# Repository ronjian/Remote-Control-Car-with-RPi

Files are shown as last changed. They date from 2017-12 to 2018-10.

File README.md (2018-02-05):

<h2 id='circuit'>Demo</h2>

<h2 id='component'>Component list</h2>

Here are the components I prepared, most I bought on Taobao. Here I give Amazon link for reference.  
- 1 * [L298N Motor Drive Controller Board](https://www.amazon.com/Qunqi-Controller-Module-Stepper-Arduino/dp/B014KMHSW6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)
- 4 * [HC-SR04 Ranging Detector / Ultrasonic Sensor](https://www.amazon.com/SainSmart-HC-SR04-Ranging-Detector-Distance/dp/B004U8TOE6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)
- 5 * [SG90 Micro Servo Motor](https://www.amazon.com/J-Deal%C2%AE-Micro-Helicopter-Airplane-Controls/dp/B00X7CJZWM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)
- 2 * [400-point Experiment Breadboard](https://www.amazon.com/microtivity-400-point-Experiment-Breadboard-Jumper/dp/B004RXKWDQ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)
- 1 * [5v 2a battery bank](https://www.amazon.com/KMASHI-15000mAh-External-Portable-Powerful/dp/B00JP8MZGK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)
- 2 * [18650 Li-ion battery](https://www.amazon.com/Panasonic-NCR18650B-Rechargeable-Battery-Transport/dp/B01C4GFVN8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)
- 1 * [Portable Wireless Bluetooth Speaker](https://www.amazon.com/A2-LENRUE-Bluetooth-Handsfree-Smartphone/dp/B071WYXY6B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)
- 1 * [RPi CSI camera](https://www.amazon.com/Arducam-Megapixels-Sensor-OV5647-Raspberry/dp/B012V1HEP4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)
- 1 * [camera extension cable 50cm](https://www.amazon.com/Miuzei-Extension-Ribbon-Raspberry-Camera/dp/B072N7VXPR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)
- 1 * [T Type GPIO Adapter](https://www.amazon.com/Kuman-Breakout-Expansion-Assembled-Raspberry/dp/B0761NYF6Y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)
- 1 * [Battery Storage Case for 2 X 18650 battery](https://www.amazon.com/SACKORANGE-Plastic-Battery-Storage-Holder/dp/B06XT1DM74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)
- 1 * [Camera Mount](https://www.amazon.com/Platform-Anti-Vibration-Dampener-Quadcopter-Crazepony/dp/B075N6TPWL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)
- 1 * [Misc, suggest such kind package](https://www.amazon.com/Elegoo-EL-CK-002-Electronic-Breadboard-Potentiometer/dp/B01ERP6WL4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)
- 1 * [RPi 3 b+](https://www.amazon.com/Raspberry-Pi-RASPBERRYPI3-MODB-1GB-Model-Motherboard/dp/B01CD5VC92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)
- 1 * RC car kit

<h2 id='circuit'>Circuit diagram</h2>

<p align="center">
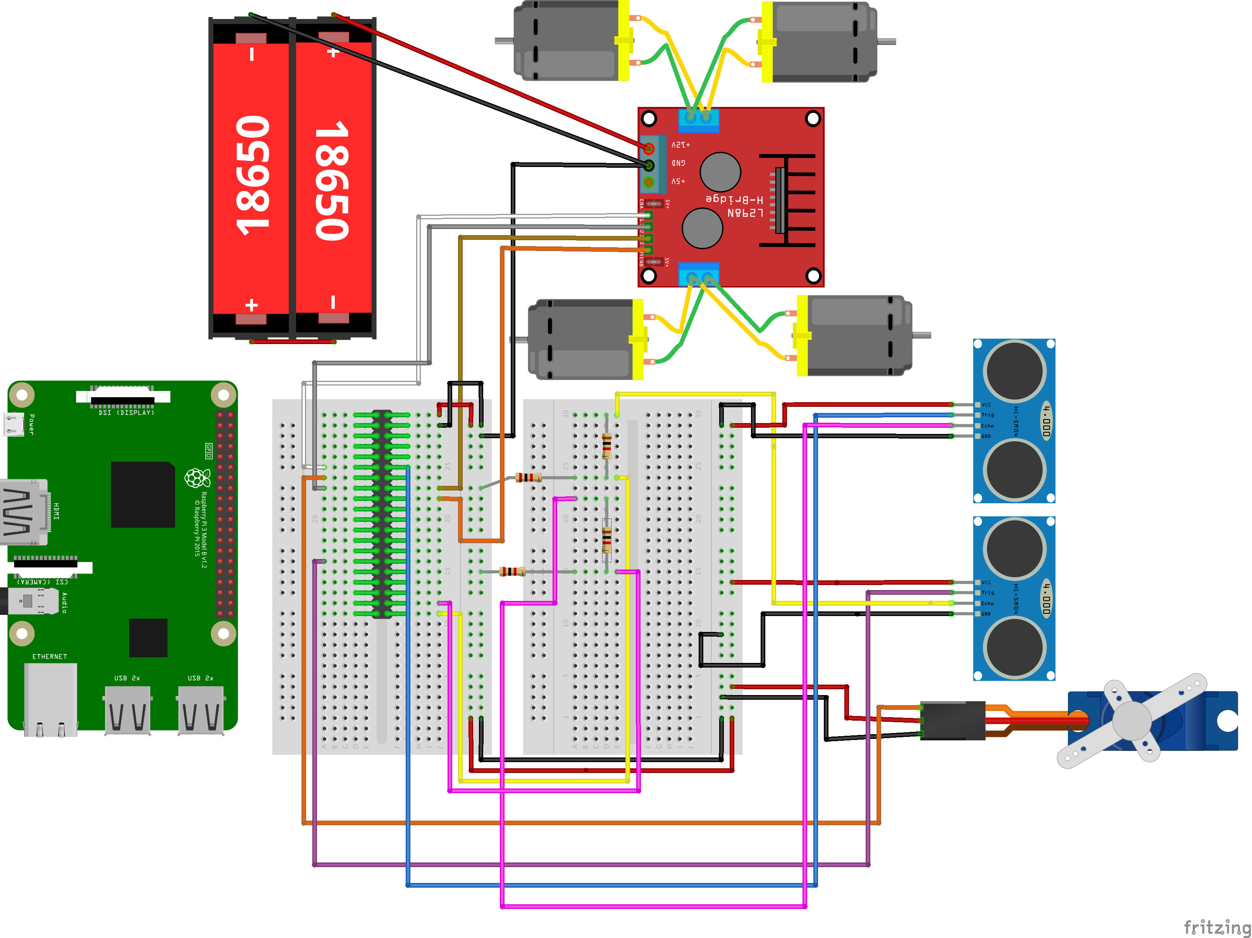
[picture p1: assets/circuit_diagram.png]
<br>
</p>

Please notes:  
- I don't draw out the audio player, camera, which are easy to be plunge in by yourself.
- I just draw out one servo and two ultra sonic sensor to keep the diagram clear.  
- In realistic, I have a T-Type GPIO Adapter like below mapping the GPIO pins to the breadboard, so in the diagram, I place a RPi header on the left side breadboard.
- [Here](./Reference.md#l298n) is more detail about L298N dirver.
- [Here](./Reference.md#HC-SR04) is more detail about HC-SR04 ultrasonic sensor.

<p align="left">
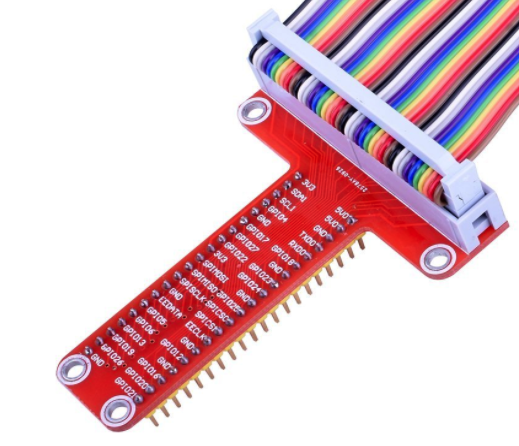
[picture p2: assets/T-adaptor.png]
<br>
</p>

I suggest checking the _Fritzing_sketch.fzz_ by [Fritzing](http://fritzing.org/home/) app.

<h2 id='introduction'>Brief introduction</h2>
This project is built on python3.  

- dependencies: [flask](http://flask.pocoo.org/), [RPi.GPIO](https://sourceforge.net/p/raspberry-gpio-python/wiki/install/), [pigpio](http://abyz.me.uk/rpi/pigpio/index.html), [picamera](https://picamera.readthedocs.io/en/release-1.13/) [pimodules](https://github.com/ronjian/pimodules)
- [Here](./Reference.md) is all the reference resources I collected during the project. Maybe you can find something I miss to mention here.
- Start server, then check ```http://192.168.1.110:2000/```(replace IP address with yours) in your browser:  
```shell
python3 ./src/main/server.py
```
- [This](./camera_streamer_manual.md) is a manual to setup mjpg steamer on RPi, which is another popular option to feed camera video. If you only want the streaming video on RPi.
- I use sublime sftp tool to sync codes between my laptop and Pi. [tutorial here](https://www.youtube.com/watch?v=g6NqBGHFfm0)

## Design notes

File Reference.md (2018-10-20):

<h2 id='gpio'>RPI3 GPIO Pin Mappings</h2>

https://pinout.xyz/

<p align="center">
<br>
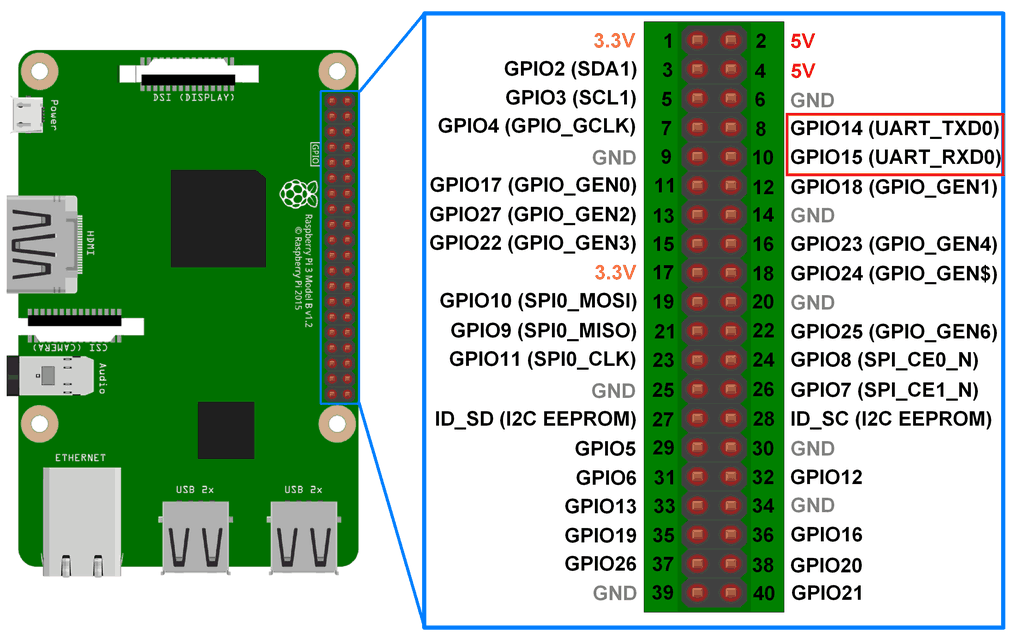
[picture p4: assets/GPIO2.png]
<br>
</p>

<h2 id='l298n'>Control motors by L298N</h2>

* Basic usage of L298N to control motors forward and backward:
    * http://www.piddlerintheroot.com/l298n-dual-h-bridge/
    * http://www.explainingcomputers.com/rasp_pi_robotics.html    
* Programming to use keyborad to control the motors:
    * Python curses package: https://docs.python.org/2/library/curses.html#constants  
    
There is two ways to control the motor speed. One is PWM changing on the INPUT pin as the below code snippet.
The other is using the enable PIN to change PWM, as [this code](https://github.com/custom-build-robots/Motor-Driver-L298N-H-Bridge/blob/master/L298NHBridge.py)
implemented. There is a [post](https://www.raspberrypi.org/forums/viewtopic.php?f=37&t=90243) comparing these two solutions.  
```python
#!/usr/bin/env python3
"""infinitely loop the motor to speed up and down"""
import time
import RPi.GPIO as GPIO
GPIO.setmode(GPIO.BCM)
GPIO.setup(23, GPIO.OUT)
GPIO.setup(24, GPIO.OUT)
p = GPIO.PWM(23, 50) 
p.start(0)
GPIO.output(24, False)
try:
    while 1:
    	# low to high
        for dc in range(0, 101, 5):
            p.ChangeDutyCycle(dc)
            time.sleep(0.2)
        # high to low
        for dc in range(100, -1, -5):
            p.ChangeDutyCycle(dc)
            time.sleep(0.2)
except KeyboardInterrupt:
    pass
p.stop()
GPIO.cleanup()
```
* check [here](http://www.toptechboy.com/raspberry-pi/raspberry-pi-lesson-27-analog-voltages-using-gpio-pwm-in-python/)
for PWM programming on RPi. [GPIO document](https://sourceforge.net/p/raspberry-gpio-python/wiki/PWM/) here.
[pigpio package](http://abyz.me.uk/rpi/pigpio/python.html) also implements controling PWM.

<h2 id='DHT11'>DHT11</h2>

Example code and tutorial:  
http://osoyoo.com/2017/03/21/%E6%A0%91%E8%8E%93%E6%B4%BE%E8%AF%BB%E5%8F%96dht11/  
<p align="center">
Diagram<br>
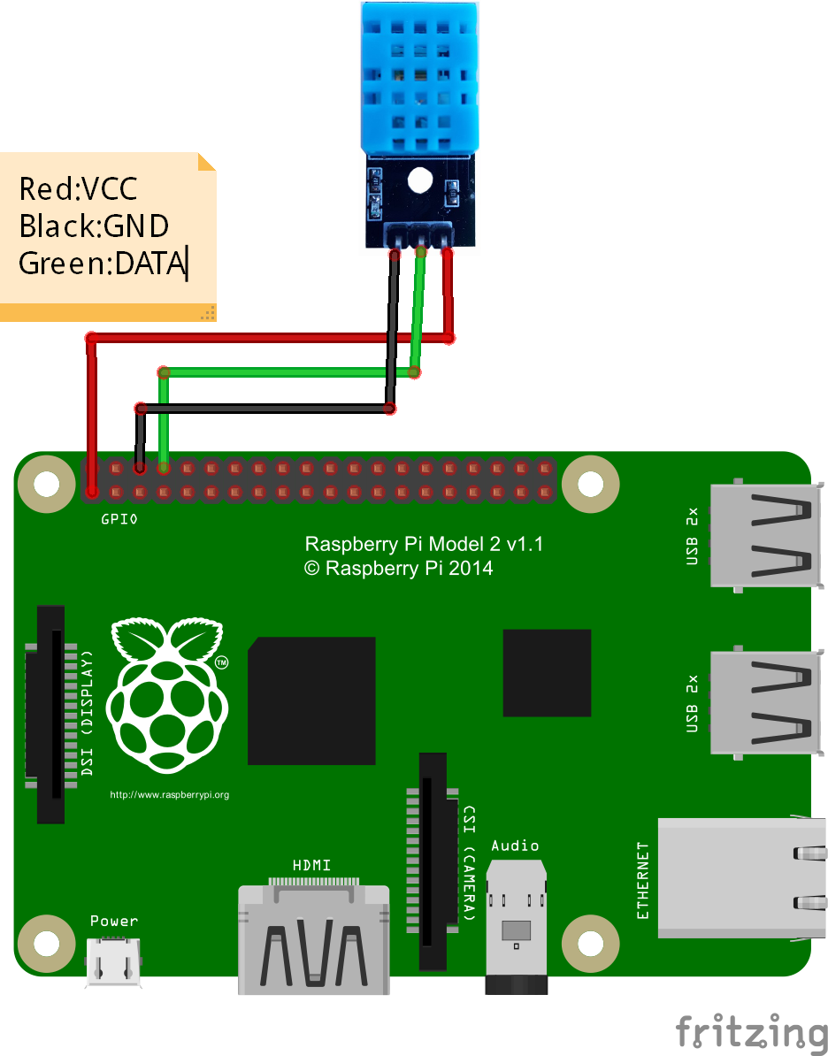
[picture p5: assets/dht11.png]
<br>
Demo<br>
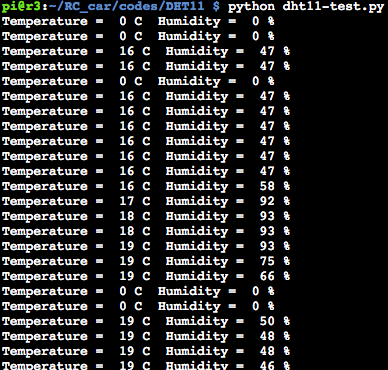
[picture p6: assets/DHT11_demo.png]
<br>
</p>

<h2 id='TCRT5000'>TCRT5000</h2>

Example code and tutorial:  
* https://raspberrytips.nl/tcrt5000/  
* https://github.com/the-raspberry-pi-guy/robot  

<p align="center">
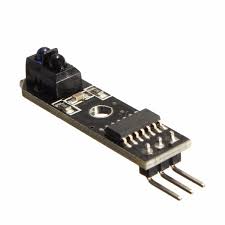
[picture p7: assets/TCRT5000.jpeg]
<br>
Demo<br>
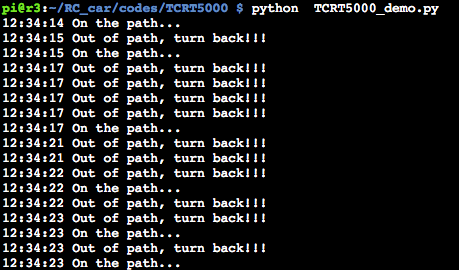
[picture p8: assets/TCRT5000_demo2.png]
<br>
</p>

<h2 id="servo">Servo</h2>

* tutorial:  
    * Servo control: https://www.youtube.com/watch?v=N5QmZ92uvUo  
    * Servo platform installation: http://v.youku.com/v_show/id_XODk3NDE1NjYw.html  

<h2 id='HC-SR04'>HC-SR04 Ultrasonic Rangefinder</h2>

reference:  
* https://www.youtube.com/watch?v=sXJjfEisjpo  
* https://www.modmypi.com/blog/hc-sr04-ultrasonic-range-sensor-on-the-raspberry-pi  
* https://raspberrytips.nl/hc-sr04-ultrasone-sensor/  
* https://gist.github.com/raspberrytipsnl/85cb7807340bede2279b12f950aef5cb  
* https://stackoverflow.com/questions/45488233/controlling-continuous-servo-using-python-in-raspberry-pi-but-the-continuous-ser

<p align="center">
Circuit diagram<br>
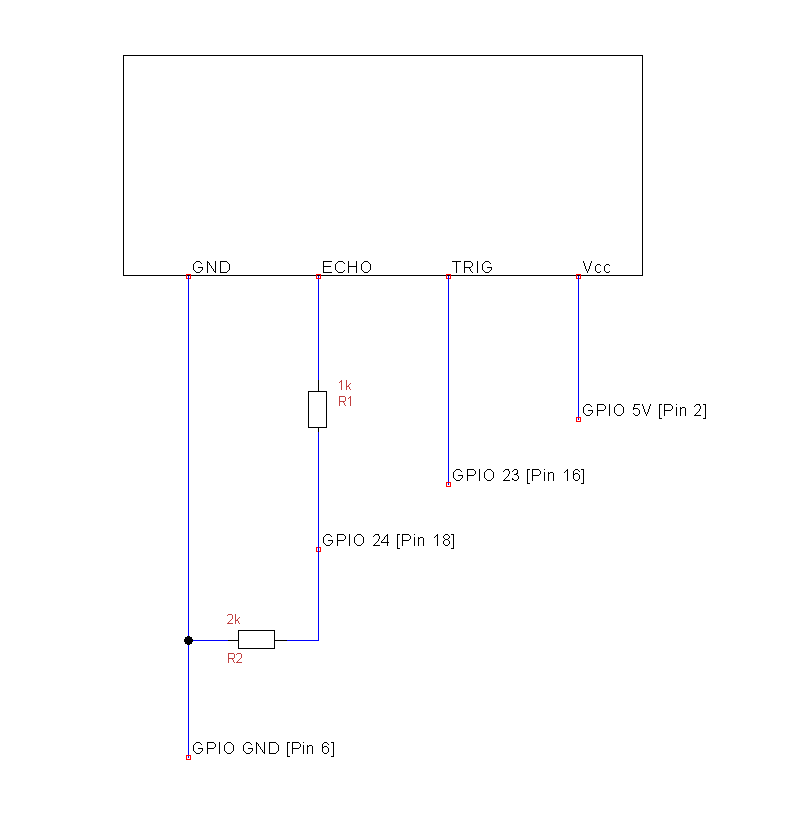
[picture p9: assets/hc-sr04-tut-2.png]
<br>
Implementation<br>
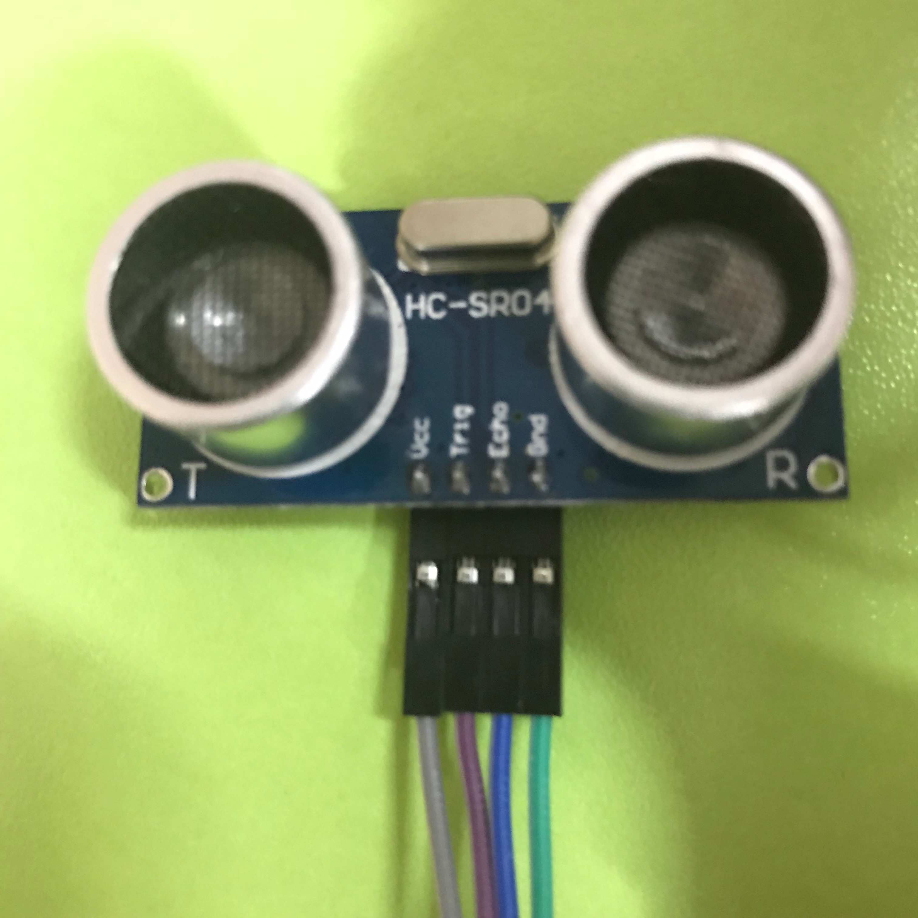
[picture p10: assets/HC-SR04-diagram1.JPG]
<br>
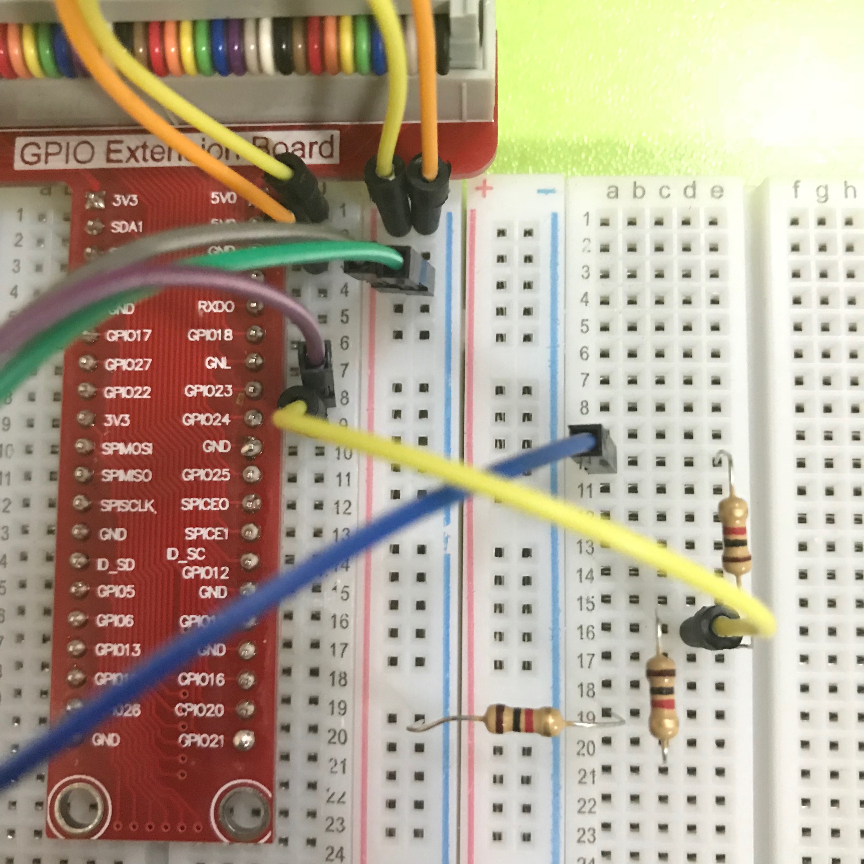
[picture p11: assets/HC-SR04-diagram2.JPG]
<br>  
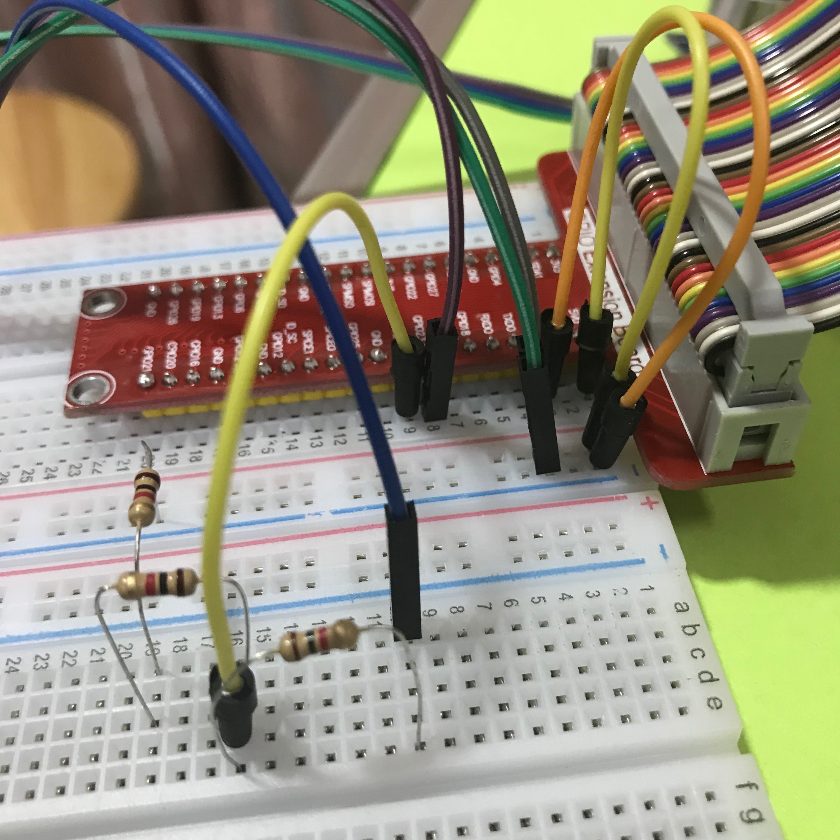
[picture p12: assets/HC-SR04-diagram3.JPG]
<br>  
Demo<br>
<br>  
</p>

<h2 id='Flask_Web_Server'>Flask Web Server</h2>

* https://randomnerdtutorials.com/raspberry-pi-web-server-using-flask-to-control-gpios/  
* http://mattrichardson.com/Raspberry-Pi-Flask/
* http://nessy.info/?p=1136
* http://vladikk.com/2013/09/12/serving-flask-with-nginx-on-ubuntu/  

<h2 id="NRF24L01">NRF24L01</h2>

* http://thezanshow.com/electronics-tutorials/raspberry-pi/tutorial-32-33  
* https://github.com/BLavery/lib_nrf24  
* SPI and I2C tutorial: https://learn.sparkfun.com/tutorials/raspberry-pi-spi-and-i2c-tutorial

<h2 id='KY-037'>KY-037</h2>

reference:  
http://sensorkit.en.joy-it.net/index.php?title=KY-037_Microphone_sensor_module_(high_sensitivity)  
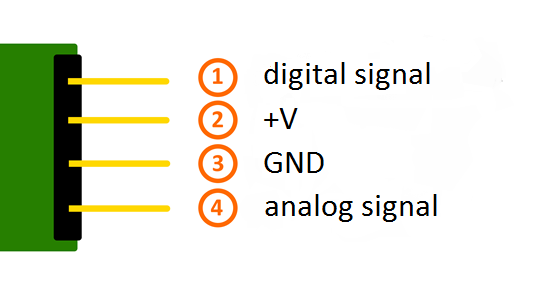
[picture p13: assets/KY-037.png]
<br>

<h2 id='FC-04'>FC-04</h2>

reference:
http://www.instructables.com/id/Using-a-sound-sensor-with-a-Raspberry-Pi-to-contro/

<h2 id='sound'>Sound Detector</h2>

reference:  
https://www.youtube.com/watch?v=GiXNUYPrQ7I  

<h2 id='heart_rate'>Heart Rate module</h2>

* MCP3008 is required
* https://pulsesensor.com/

<h2 id='speaking'>Make RPi speak</h2>

Setting ```audio_pwm_mode=2``` in ```/boot/config.txt``` can reduce the background noise for audio from 3.5mm jack.

If you want to set usb sound card for RPi3 as default sound output.  
- check the device number by ```aplay -l```  
- add below lines to ```/etc/asound.conf```   
```
pcm.!default {
    type hw
    card 1
}

ctl.!default {
    type hw           
    card 1
}
```

- verify as:

```aplay -D plughw:1,0  /usr/share/sounds/alsa/*```

```omxplayer -b -o alsa:hw:1,0  xxx.mp3```

Install ```espeak``` on RPi, refer to: 

- https://www.dexterindustries.com/howto/make-your-raspberry-pi-speak/
- https://www.devdungeon.com/content/text-speech-python-espeak

- volumn control:  
http://blog.scphillips.com/posts/2013/01/sound-configuration-on-raspberry-pi-with-alsa/

- Install espeak lib for python3 as 
```sudo apt-get install espeak python-espeak```

<h2 id='pi-shutdown-button'>Control Pi start, shutdown, reboot with one button</h2>

- https://gilyes.com/pi-shutdown-button/
- threaded callback function: https://sourceforge.net/p/raspberry-gpio-python/wiki/Inputs/

<h2 id="camera">Camera</h2>

- Amazing recipes for RPi camera: https://picamera.readthedocs.io/en/release-1.13/recipes1.html
- Flask server solution to stream camera video: https://github.com/miguelgrinberg/flask-video-streaming

<h2 id='KY-022'>KY-022(IR sensor)</h2>

reference:  
- wire connection: http://sensorkit.en.joy-it.net/index.php?title=KY-022_Infrared_receiver_module#Code_example_Raspberry_Pi
- IR receiver code in python: http://abyz.me.uk/rpi/pigpio/examples.html#Python%20code (see "IR Receiver")

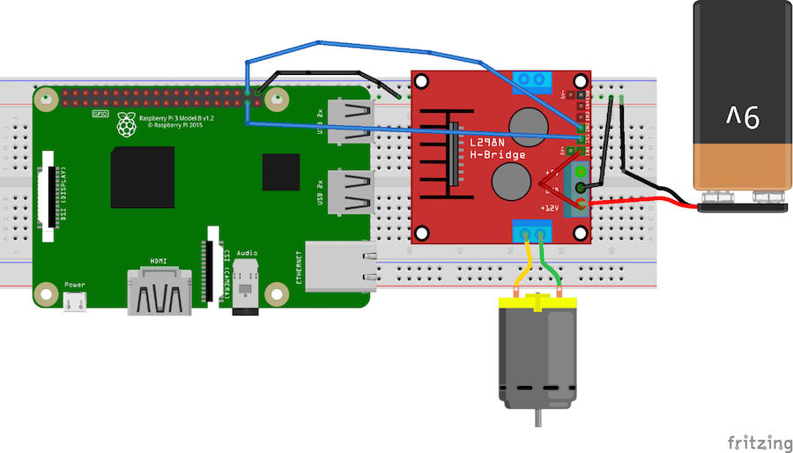
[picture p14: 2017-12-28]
assets/Raspberry-Pi-L298-Schematic.png

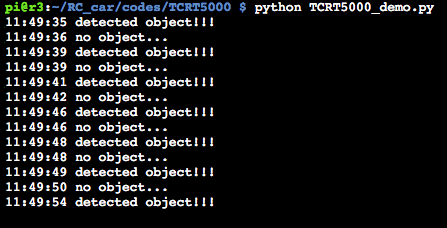
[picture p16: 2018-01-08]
assets/TCRT5000_demo.png

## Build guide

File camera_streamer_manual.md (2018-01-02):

# Steps to stream the Raspberry Pi camera video to client browser in the WIFI enviroment.
Refer to this post for detail: http://petrkout.com/electronics/low-latency-0-4-s-video-streaming-from-raspberry-pi-mjpeg-streamer-opencv/  
Do below steps on the Raspberry Pi (Mine is Raspberry Pi 3 Model B):  
```shell
mkdir mjpg-streamer
cd mjpg-streamer
git clone https://github.com/jacksonliam/mjpg-streamer.git .
cd mjpg-streamer-experimental
make
export LD_LIBRARY_PATH=.
./mjpg_streamer -o "output_http.so -w ./www" -i "input_raspicam.so -x 640 -y 480 -fps 20 -ex night -rot 180"
```  
Check the browser via url ```http://r3:8080/?action=stream```, 
```r3``` is my Pi's hostname in the internel network, Ip address like ```192.168.31.110``` also works fine.  
### Demo:
<p align="center">
<img src="assets/infinite.png" width=700/>
<p/>

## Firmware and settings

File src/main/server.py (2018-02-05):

from flask import Flask, render_template, request, Response
from pimodules import motor, servo_hw, ultrasonic
import obstacle_avoidance
from time import sleep
import threading
from pathlib import Path
from camera.camera_pi import Camera

app = Flask(__name__)

@app.route("/")
def index():
    return render_template('index.html')

def gen(camera):
    """Video streaming generator function."""
    while True:
        frame = camera.get_frame()
        yield (b'--frame\r\n'
               b'Content-Type: image/jpeg\r\n\r\n' + frame + b'\r\n')

@app.route('/video_feed')
def video_feed():
    """Video streaming route. Put this in the src attribute of an img tag."""
    return Response(gen(Camera()),
                    mimetype='multipart/x-mixed-replace; boundary=frame')

@app.route("/forward")
def forward():
    speed_pct = int(request.args.get('speed_pct'))
    motor_control.forward(speed_pct)
    return "OK"
 
@app.route("/backward")
def backward():
    speed_pct = int(request.args.get('speed_pct'))
    motor_control.backward(speed_pct)
    return "OK"

@app.route("/turn_left")
def turn_left():
    speed_pct = int(request.args.get('speed_pct'))
    motor_control.left(speed_pct)
    return "OK"
 
@app.route("/turn_right")
def turn_right():
    speed_pct = int(request.args.get('speed_pct'))
    motor_control.right(speed_pct)
    return "OK"

@app.route("/stop")
def stop():
    motor_control.stop()
    return "OK"

@app.route("/camera_up")
def camera_up():
    camera_vertical_servo.step_move(direction = -1.0)
    return "OK"
 
@app.route("/camera_down")
def camera_down():
    camera_vertical_servo.step_move(direction = 1.0)
    return "OK"

@app.route("/camera_left")
def camera_left():
    camera_horizontal_servo.step_move(direction = 1.0)
    return "OK"
 
@app.route("/camera_right")
def camera_right():
    camera_horizontal_servo.step_move(direction = -1.0)
    return "OK"

@app.route("/camera_reset")
def camera_reset():
    camera_vertical_servo.reset()
    camera_horizontal_servo.reset()
    return "OK"

@app.route("/take_photo")
def take_photo():
    pass
    return "OK"

@app.route("/back_uc_left")
def back_uc_left():
    back_servo.step_move(direction = 1.0)
    return "OK"
 
@app.route("/back_uc_right")
def back_uc_right():
    back_servo.step_move(direction = -1.0)
    return "OK"

@app.route("/back_uc_reset")
def back_uc_reset():
    back_servo.reset()
    return "OK"

@app.route("/back_distance")
def back_distance():
    print("Back distance is %f cm" % back_ultrasonic.detect())
    return "OK"

@app.route("/left_uc_left")
def left_uc_left():
    left_servo.step_move(direction = 1.0)
    return "OK"
 
@app.route("/left_uc_right")
def left_uc_right():
    left_servo.step_move(direction = -1.0)
    return "OK"

@app.route("/left_uc_reset")
def left_uc_reset():
    left_servo.reset()
    return "OK"

@app.route("/left_distance")
def left_distance():
    print("Left distance is %f cm" % left_ultrasonic.detect())
    return "OK"

@app.route("/right_uc_left")
def right_uc_left():
    right_servo.step_move(direction = 1.0)
    return "OK"
 
@app.route("/right_uc_right")
def right_uc_right():
    right_servo.step_move(direction = -1.0)
    return "OK"

@app.route("/right_uc_reset")
def right_uc_reset():
    right_servo.reset()
    return "OK"

@app.route("/right_distance")
def right_distance():
    print("Right distance is %f cm" % right_ultrasonic.detect())
    return "OK"

@app.route("/obstacle_avoiding_start")
def obstacle_avoiding_start():
    stop_instances()
    if oa_signal_path.exists(): oa_signal_path.unlink()
    t = threading.Thread(target=obstacle_avoidance.start)
    t.start()
    print("thread kick off")
    return "OK"

@app.route("/obstacle_avoiding_stop")
def obstacle_avoiding_stop(restart=True):
    oa_signal_path.touch()
    print("sent the stop signal")
    if restart:
        while oa_signal_path.exists():
            sleep(1)
        print("obstacle_avoiding stopped, restarting instances")
        start_instances()
    return "OK"

def start_instances():
    motor_control.start()
    back_ultrasonic.start()
    right_ultrasonic.start()
    left_ultrasonic.start()
    right_servo.start()
    camera_vertical_servo.start()
    camera_horizontal_servo.start()
    left_servo.start()
    back_servo.start()
    
def stop_instances():
    # make sure to close servos first
    camera_vertical_servo.close()
    camera_horizontal_servo.close()
    back_servo.close()
    left_servo.close()
    right_servo.close()
    right_ultrasonic.close()
    motor_control.close()
    back_ultrasonic.close()
    left_ultrasonic.close()

if __name__ == "__main__":
    try:
        STRIDE=0.05
        motor_control = motor.CONTROL(RIGHT_FRONT_PIN=17, LEFT_FRONT_PIN=23, RIGHT_BACK_PIN=22, LEFT_BACK_PIN=24)
        back_ultrasonic = ultrasonic.CONTROL(TRIG = 6, ECHO = 13)
        right_ultrasonic = ultrasonic.CONTROL(TRIG = 5, ECHO = 21)
        left_ultrasonic = ultrasonic.CONTROL(TRIG = 25, ECHO = 20)

        camera_vertical_servo = servo_hw.CONTROL(PIN=26,STRIDE= STRIDE)
        camera_horizontal_servo = servo_hw.CONTROL(PIN=19,STRIDE= STRIDE)
        back_servo = servo_hw.CONTROL(PIN=18,STRIDE= STRIDE,RANGE=100)
        left_servo = servo_hw.CONTROL(PIN=4,STRIDE= STRIDE)
        right_servo = servo_hw.CONTROL(PIN=27,STRIDE= STRIDE)

        oa_signal_path = Path('data/obstacle_avoidance_exit.signal')
        
        app.run(host='0.0.0.0', port=2000, debug=False, threaded=True)

    finally:
        print("Clearing")
        stop_instances()
        print("Bye!")

    

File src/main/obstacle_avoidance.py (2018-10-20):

from pimodules import motor, servo_hw
from time import sleep
from pathlib import Path
import pigpio
import ultrasonic_pigpio_left as left
import ultrasonic_pigpio_right as right
import ultrasonic_pigpio_front as front

def __avg_distance(obj):
	record = []
	for i in range(3):
		record.append(obj.readDistance())
	record.sort()
	dis=record[1]
	return dis

def tune_servo( uc):
	front_done=False
	front_pos = 0.0
	while not front_done :
		uc.direct_move(front_pos,given_time = 1.0)
		input_txt = input("now front position is %f, enter number to tune or enter to done: " % front_pos)
		if input_txt == "": 
			front_done = True
		else :
			front_pos = float(input_txt)
	side_done=False
	side_pos = 0.0
	while not side_done :
		uc.direct_move(side_pos,given_time = 1.0)
		input_txt = input("now side position is %f, enter number to tune or enter to done: " % side_pos)
		if input_txt == "": 
			side_done = True
		else :
			side_pos = float(input_txt)
	return front_pos, side_pos

def __uc_scan( uc, obj, front, side):
	# from front to side
	min_dis = 400 # start at max limitation
	step = (side - front) / 10.0
	pos = front
	uc.direct_move(pos,given_time = 0.3)
	while (front <= pos and pos <= side ) or (front >= pos and pos >= side ):
		pos += step
		uc.direct_move(pos,given_time = 0.15)
		dis = __avg_distance(obj)
		if dis < min_dis:
			min_dis = dis
			ref_pos = pos
	uc.direct_move(ref_pos,given_time = 0.3)
	return min_dis , ref_pos

def start():
	oa_signal_path = Path('data/obstacle_avoidance_exit.signal')
	# kick off all instances
	# motor control
	mc = motor.CONTROL(RIGHT_FRONT_PIN=17, 
						LEFT_FRONT_PIN=23, 
						RIGHT_BACK_PIN=22, 
						LEFT_BACK_PIN=24)
	# left servo
	left_uc = servo_hw.CONTROL(PIN=4)
	# right servo
	right_uc = servo_hw.CONTROL(PIN=27)
	# # left ultrasonic
	# left_ud = ultrasonic.CONTROL(TRIG = 25, ECHO = 20)
	# # right ultrasonic
	# right_ud = ultrasonic.CONTROL(TRIG = 5, ECHO = 21)
	# # front ultrasonic
	# front_ud = ultrasonic.CONTROL(TRIG = 16, ECHO = 12)
	# left_echo1 = pi.callback(20, pigpio.RISING_EDGE,  _echo1)
	# left_echo0 = pi.callback(20, pigpio.FALLING_EDGE, _echo0)
	# right_echo1 = pi.callback(21, pigpio.RISING_EDGE,  _echo1)
	# right_echo0 = pi.callback(21, pigpio.FALLING_EDGE, _echo0)
	# front_echo1 = pi.callback(12, pigpio.RISING_EDGE,  _echo1)
	# front_echo0 = pi.callback(12, pigpio.FALLING_EDGE, _echo0)

	LEFT_FRONT_DC, LEFT_SIDE_DC =  1250, 2200 # tune_servo(left_uc)
	RIGHT_FRONT_DC, RIGHT_SIDE_DC = 1900, 900  # tune_servo(right_uc)
	side_threshold=15 # cm
	front_threshold=25 # cm
	turn_threshold = 6 # cm
	speed = 50
	try:
		forward=False
		turn_flag="left"
		while True:
			# seek path
			if forward==False:
				# check exit signal
				if oa_signal_path.exists():
					break
				else:
					right_danger, right_ref_pos = __uc_scan(right_uc, right, RIGHT_FRONT_DC, RIGHT_SIDE_DC)
					print("right min distance is %f cm" % right_danger)
					left_danger, left_ref_pos = __uc_scan(left_uc, left, LEFT_FRONT_DC, LEFT_SIDE_DC)
					print("left min distance is %f cm" % left_danger )

					front_danger = __avg_distance(front)
					print("front danger is %f cm " % front_danger)
					if right_danger > side_threshold and left_danger > side_threshold and front_danger>front_threshold:
						print("Go!")
						mc.forward(speed)
						forward=True
					else:
						if left_danger < turn_threshold and turn_flag == "left" :
							turn_flag = "right"
						elif right_danger < turn_threshold and turn_flag == "right" :
							turn_flag = "left"

						if turn_flag == "left":
							print("turn left")
							mc.left(speed)
							sleep(0.3)
							mc.stop()
						else:
							print("turn right")
							mc.right(speed)
							sleep(0.3)
							mc.stop()
			# monitor danger
			else:
				left_danger = __avg_distance(left)
				right_danger = __avg_distance(right)
				front_danger = __avg_distance(front)
				if left_danger < side_threshold or right_danger < side_threshold or front_danger < front_threshold:
						print("Stop!")
						mc.stop()
						forward=False
				sleep(0.01)
	except Exception as e:
		print(str(e))
	finally:
		# clear
		left_uc.close()
		right_uc.close()
		mc.close()
		# left_ud.close()
		# right_ud.close()
		# front_ud.close()
		if oa_signal_path.exists():oa_signal_path.unlink()
		print("exit obstacle avoidance mode")

if __name__ == "__main__":
	start()

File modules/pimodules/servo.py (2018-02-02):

import RPi.GPIO as GPIO  
from time import sleep

class CONTROL:
	"""
	This module abstract the action of a typical servo: 
	1. little step cycle in two opposite direction choices
	2. direct cycle to specific angle
	3. reset to initial angle

	Be careful to set the range to protest your servo.
	"""
	def __init__(self, PIN, STRIDE= 0.01, NOMINAL=7.5, RANGE=3.9):
		self.STRIDE= STRIDE # step magnitude
		self.NOMINAL= NOMINAL  # initial digital cycle/angle
		self.RANGE = RANGE  # range limitation
		self.previous_dc = self.NOMINAL # tracking the previous angle
		self.MAX_DC = self.NOMINAL +  self.RANGE # high limit
		self.MIN_DC = self.NOMINAL -  self.RANGE # low limit
		self.PIN = PIN
		self.start()

	def start(self):
		GPIO.setmode(GPIO.BCM)
		GPIO.setup(self.PIN, GPIO.OUT, initial=False)  
		self.PWM = GPIO.PWM(self.PIN,50)
		self.PWM.start(self.NOMINAL)
		# give time to cycle
		sleep(1)

	def step_move(self,direction=1.0):
		"""
		Cycle servo a little step.
		This function can only control the direction.

		Limit: servo can't cycle out of the given range.

		:param direction: 1.0 or -1.0
		"""
		dc = self.previous_dc + direction * self.RANGE * self.STRIDE
		if dc > self.MAX_DC or dc < self.MIN_DC:
			print("WARNING!! The servo reached the limit.")
		else:
			self.PWM.ChangeDutyCycle(dc)  
			self.previous_dc = dc


	def direct_move(self, dc, given_time = 1.0):
		"""
		Cycle the servo directly to specific angle.
		The servo works in async with this function.
		Make sure giving the servo some time to move
		before giving it other commands.
		
		Limit: servo can't cycle out of the given range.

		:param dc: digital cycle, can be treat as postion 
		of ther servo
		:param given_time: give servo time to cycle 
		to position

		"""
		if dc > self.MAX_DC:
			print("WARNING!! {} is higher than the high limit {}".format(dc, self.MAX_DC))
			dc = self.MAX_DC
		elif dc < self.MIN_DC:
			print("WARNING!! {} is lower than the low limit {}".format(dc, self.MIN_DC))
			dc = self.MIN_DC
			
		self.PWM.ChangeDutyCycle(dc)
		if given_time > 0.0: sleep(given_time)
		self.previous_dc = dc


	def reset(self):
		"""
		reset to initial angle
		"""
		self.direct_move(self.NOMINAL)

	def stop(self, reset=True):
		"""
		make sure to invoke this function 
		to quit your program elegantly
		"""
		if reset:
			self.reset()
		self.PWM.stop()

	def close(self, reset=True):
		self.stop(reset=reset)
		GPIO.cleanup()

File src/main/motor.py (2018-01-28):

#!/usr/bin/env python3
import RPi.GPIO as GPIO

class CONTROL:

	def __init__(self, RIGHT_FRONT_PIN,\
						LEFT_FRONT_PIN,\
						RIGHT_BACK_PIN,\
						LEFT_BACK_PIN,\
						FREQUENCY=2000):
		self.RIGHT_FRONT_PIN = RIGHT_FRONT_PIN
		self.LEFT_FRONT_PIN = LEFT_FRONT_PIN
		self.RIGHT_BACK_PIN = RIGHT_BACK_PIN
		self.LEFT_BACK_PIN = LEFT_BACK_PIN
		self.FREQUENCY = FREQUENCY
		self.start()

	def start(self):
		GPIO.setmode(GPIO.BCM)
		GPIO.setup(self.RIGHT_FRONT_PIN, GPIO.OUT)
		GPIO.setup(self.RIGHT_BACK_PIN, GPIO.OUT)
		GPIO.setup(self.LEFT_FRONT_PIN, GPIO.OUT)
		GPIO.setup(self.LEFT_BACK_PIN, GPIO.OUT)
		self.right_forward = GPIO.PWM(self.RIGHT_FRONT_PIN, self.FREQUENCY) 
		self.right_forward.start(0)
		self.right_backward = GPIO.PWM(self.RIGHT_BACK_PIN, self.FREQUENCY) 
		self.right_backward.start(0)
		self.left_forward = GPIO.PWM(self.LEFT_FRONT_PIN, self.FREQUENCY) 
		self.left_forward.start(0)
		self.left_backward = GPIO.PWM(self.LEFT_BACK_PIN, self.FREQUENCY) 
		self.left_backward.start(0)

	def stop(self):
		"""stop car"""
		self.left_forward.ChangeDutyCycle(0)
		self.left_backward.ChangeDutyCycle(0)
		self.right_forward.ChangeDutyCycle(0)
		self.right_backward.ChangeDutyCycle(0)

	def __inner_right(self, dc_pct=100.0):
		"""
		Control left side wheels

		Args:

		"""
		if dc_pct > 0 :
			self.right_forward.ChangeDutyCycle(dc_pct)
		else:
			self.right_backward.ChangeDutyCycle(-1 * dc_pct)

	def __inner_left(self, dc_pct=100.0):
		"""
		Control right side wheels

		Args:

		"""
		if dc_pct > 0 :
			self.left_forward.ChangeDutyCycle(dc_pct)
		else:
			self.left_backward.ChangeDutyCycle(-1 * dc_pct)


	def forward(self, dc_pct=100.0):
		"""
		Control both side wheels to cycle forward.

		Args:

		"""
		self.stop()
		self.__inner_right(dc_pct)
		self.__inner_left(dc_pct)

	def backward(self, dc_pct=100.0):
		"""
		Control both side wheels to cycle in the same direction.

		Args:

		"""
		self.stop()
		self.forward(-1 * dc_pct)


	def left(self, dc_pct=100.0):
		"""
		Control two sides wheels to cycle in opposite direction
		 to make the car cycling.

		Args:

		"""
		self.stop()
		self.__inner_left(dc_pct)
		self.__inner_right(-1 * dc_pct)

	def right(self, dc_pct=100.0):
		"""
		Control two sides wheels to cycle in opposite direction
		 to make the car cycling.

		Args:

		"""
		self.stop()
		self.left(-1 * dc_pct)

	def close(self):
		GPIO.cleanup()

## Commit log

2018-01-09 build camera servo
2018-01-10 PWM controling motor speed function tests successfully
2018-01-14 add camera module
2018-01-15 add left and right ultrasonic sensor
2018-01-28 clear project structure
    [Fritzing_sketch.fzz]
2018-01-29 integrate obstacle avoidance into web server complete 70%
    [obstacle_avoidance.py, server.py, servo.py]
2018-01-30 integrate obstacle avoidance into web server, complete 100%
    [obstacle_avoidance.py, server.py, servo.py]
2018-02-02 - modulize low level operation on GPIO - change the camera streaming solution from mjpeg streamer to naive picamera module, and integrate the server part into flask app server - improve markdown file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
2018-02-03 change servos from software PWM to hardware PWM
